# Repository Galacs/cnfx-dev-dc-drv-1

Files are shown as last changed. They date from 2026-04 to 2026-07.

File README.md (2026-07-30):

# CNFX Dev DC Driver 1

Dual 5V 1.5A DC motor driver for the cnfx series

## IC List

- STM32F103C8T6 (Main MCU)
- HT7533 (MCU 3v3 LDO)
- SN65HVD230DR (CAN transceiver)
- WS2812B (RGB addressable led)
- TPS259472 (+5V input efuse)
- DRV8837 (Integrated H-Bridge)

## Top preview



## Preview 3d render



## Pin definitions

```c

#define CAN_TX_PIN PA12
#define CAN_RX_PIN PA11
#define CAN_STATUS_PIN PA15

#define RGB_PIN PB13
#define ILM_PIN PB0
#define BTN_PIN PB12

#define SEL_0_PIN PB5
#define SEL_1_PIN PB6
#define SEL_2_PIN PB7

#define DC_1_SLEEP PA5
#define DC_1_IN1 PA6
#define DC_1_IN2 PA7

#define DC_1_SLEEP PA0
#define DC_1_IN1 PA1
#define DC_1_IN2 PA2
```

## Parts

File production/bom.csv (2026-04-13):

Designator | Footprint | Quantity | Value | LCSC Part #
C1, C16, C17 | 0402 | 3 | 1u | C52923
C10, C9 | 0603 | 2 | 20p | C1648
C11, C12, C14, C15, C18, C2, C21, C7 | 0402 | 8 | 0u1 | C307331
C13, C6, C8 | 0805 | 3 | 10u | C440198
C19, C20, C22, C23, C5 | 0805 | 5 | 22u | C45783
C4 | 0402 | 1 | 1n | C1523
D1 | LED_WS2812B_PLCC4_5.0x5.0mm_P3.2mm | 1 | WS2812B | C2874885
D2, D3, D4, D5, D7 | Diode_DFN1006 | 5 | H5VU10U | C22395519
D6 | 0805 | 1 | GREEN | C2297
D8 | 0805 | 1 | YELLOW | C2296
FB1 | 0805 | 1 | 600Ω@100M | C81034
J1 | JST_XH_B3B-XH-A_1x03_P2.50mm_Vertical | 1 | Conn_01x03
J3, J4, J6, J7 | JST_XH_B2B-XH-A_1x02_P2.50mm_Vertical | 4 | Conn_01x02
JP2, JP3, JP4 | SolderJumper-2_P1.3mm_Open_RoundedPad1.0x1.5mm | 3 | Jumper_2_Open
R1 | 1206 | 1 | 120 | C17909
R2 | 0402 | 1 | 820 | C25135
R3, R5, R8 | 0402 | 3 | 5k1 | C25905
R4, R6 | 0402 | 2 | 10k | C25744
R7 | 0603 | 1 | 560 | C23204
SW1, SW2, SW3 | SW_SPST_TS-1088-xR020 | 3 | SW_Push | C720477
TP1, TP2 | TestPoint_Keystone_5015_Micro_Mini | 2 | TestPoint | C2906768
U1 | SOIC-8_3.9x4.9mm_P1.27mm | 1 | SN65HVD230 | C12084
U2 | Texas_RPW0010A_VQFN-HR-10_2x2mm_P0.5mm | 1 | TPS259472A | C3662789
U3 | SOT-89-3 | 1 | HT753-1 | C14289
U4 | LQFP-48_7x7mm_P0.5mm | 1 | STM32F103C8Tx | C8734
U5, U6 | WSON-8-1EP_2x2mm_P0.5mm_EP0.9x1.6mm | 2 | DRV8837 | C39159
Y1 | Crystal_SMD_5032-2Pin_5.0x3.2mm | 1 | 8M | C115962

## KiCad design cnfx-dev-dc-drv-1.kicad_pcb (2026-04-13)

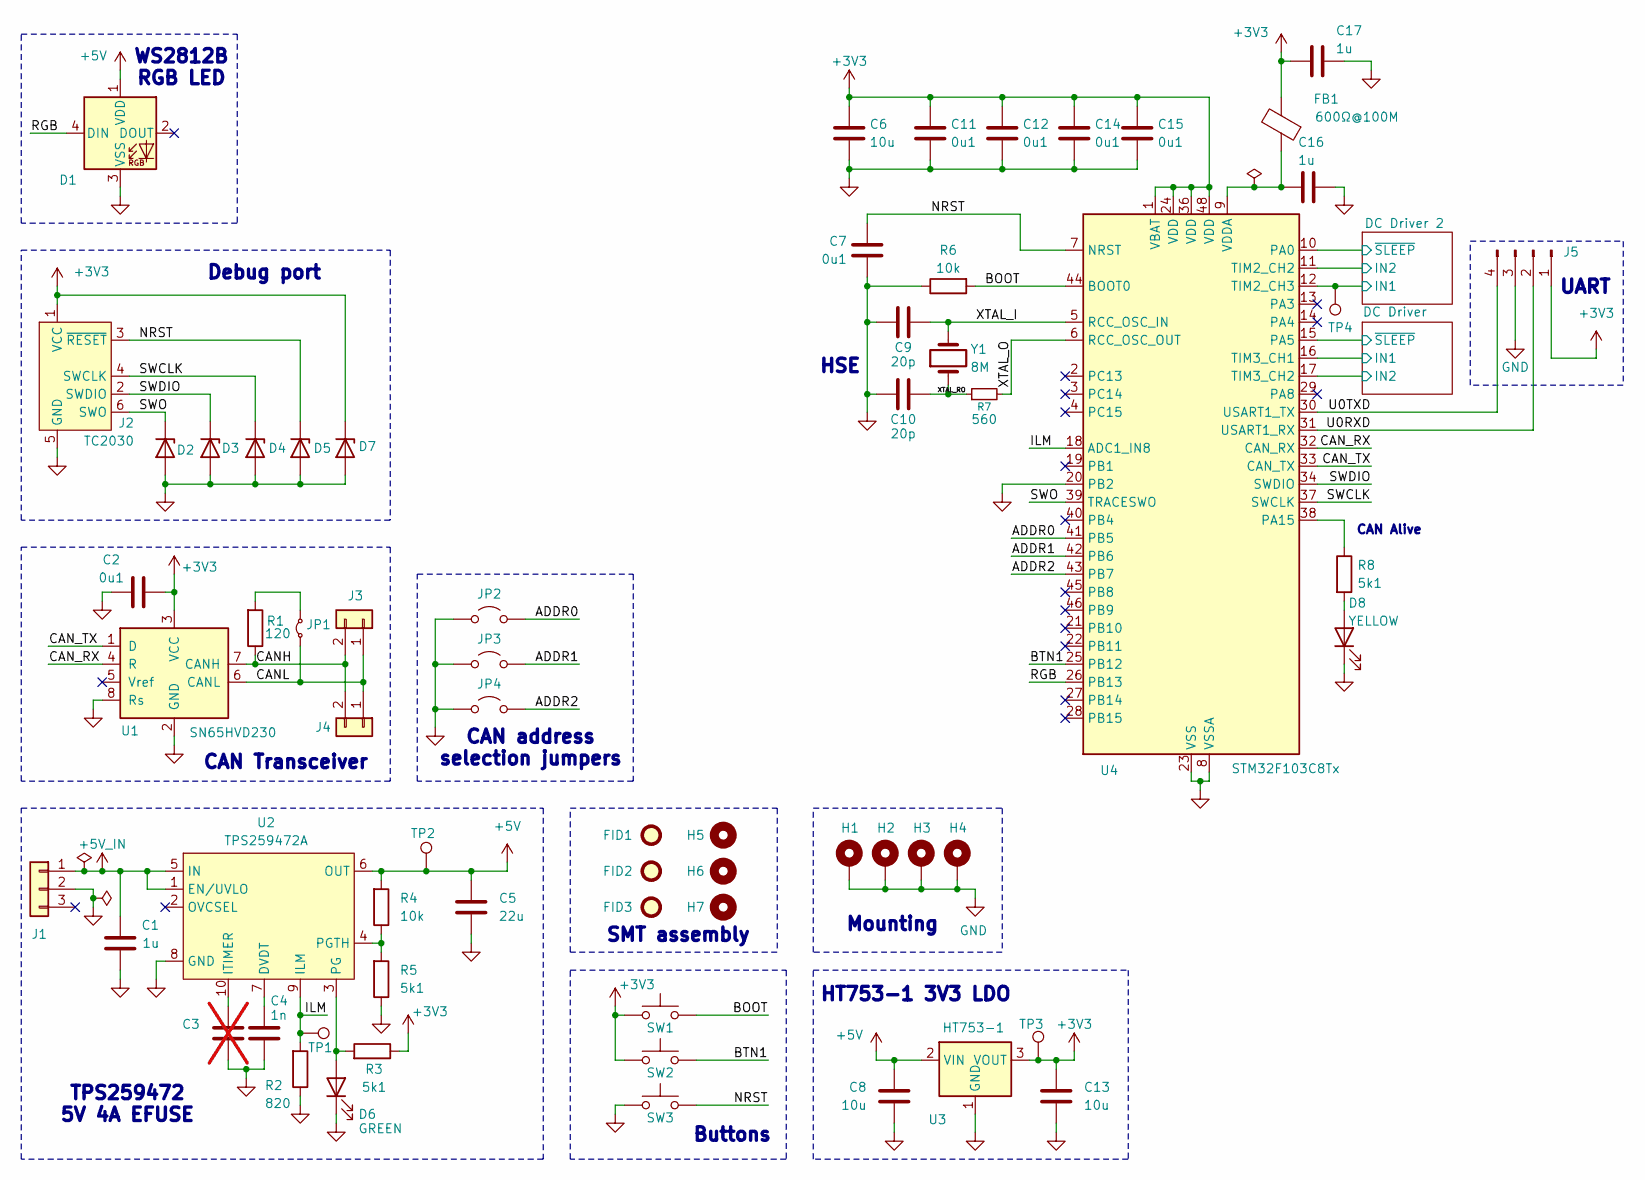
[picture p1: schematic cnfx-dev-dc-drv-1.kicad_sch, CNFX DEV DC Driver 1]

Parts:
C1, C16, C17: 1u; C_0402_1005Metric; Manufacturer Part Number CL05A105KA5NQNC; JLCPCB Part # C52923
C2, C7, C11, C12, C14, C15: 0u1; C_0402_1005Metric; Manufacturer Part Number CL05B104KB54PNC; JLCPCB Part # C307331
C3: C; C_0402_1005Metric; not fitted
C4: 1n; C_0402_1005Metric; Manufacturer Part Number 0402B102K500NT; JLCPCB Part # C1523
C5: 22u; C_0805_2012Metric; Manufacturer Part Number CL21A226MAQNNNE; JLCPCB Part # C45783
C6, C8, C13: 10u; C_0805_2012Metric; Manufacturer Part Number GRM21BR61H106KE43L; JLCPCB Part # C440198
C9, C10: 20p; C_0603_1608Metric; Manufacturer Part Number CL10C200JB8NNNC; JLCPCB Part # C1648
D1: WS2812B; LED_WS2812B_PLCC4_5.0x5.0mm_P3.2mm; Manufacturer Part Number WS2812B-V5/W; JLCPCB Part # C2874885
D2, D3, D4, D5, D7: H5VU10U; Diode_DFN1006; Manufacturer Part Number H5VU10U; JLCPCB Part # C22395519
D6: GREEN; LED_0805_2012Metric; Manufacturer Part Number KT-0805G; JLCPCB Part # C2297
D8: YELLOW; LED_0805_2012Metric; Manufacturer Part Number KT-0805Y; JLCPCB Part # C2296
FB1: 600Ω@100M; L_0805_2012Metric; Manufacturer Part Number MPZ2012S601ATD25; JLCPCB Part # C81034
FID1, FID2, FID3: Fiducial; Fiducial_1mm_Mask2mm
H1, H2, H3, H4: MountingHole_Pad; MountingHole_3.2mm_M3_Pad_Via
H5, H6, H7: MountingHole; ToolingHole_1.152mm
J1: Conn_01x03; JST_XH_B3B-XH-A_1x03_P2.50mm_Vertical
J2: TC2030; Tag-Connect_TC2030-IDC-NL_2x03_P1.27mm_Vertical
J3, J4: Conn_01x02; JST_XH_B2B-XH-A_1x02_P2.50mm_Vertical
J5: Conn_01x04_Pin; PinHeader_1x04_P2.54mm_Vertical
JP1: Jumper_2_Small_Bridged; PinHeader_1x02_P2.54mm_Vertical
JP2, JP3, JP4: Jumper_2_Open; SolderJumper-2_P1.3mm_Open_RoundedPad1.0x1.5mm
R1: 120; R_1206_3216Metric; Manufacturer Part Number 1206W4F1200T5E; JLCPCB Part # C17909
R2: 820; R_0402_1005Metric; Manufacturer Part Number 0402WGF8200TCE; JLCPCB Part # C25135
R3, R5, R8: 5k1; R_0402_1005Metric; Manufacturer Part Number 0402WGF5101TCE; JLCPCB Part # C25905
R4, R6: 10k; R_0402_1005Metric; Manufacturer Part Number 0402WGF1002TCE; JLCPCB Part # C25744
R7: 560; R_0603_1608Metric; Manufacturer Part Number 0603WAF5600T5E; JLCPCB Part # C23204
SW1, SW2, SW3: SW_Push; SW_SPST_TS-1088-xR020; Manufacturer Part Number TS-1088-AR02016; JLCPCB Part # C720477
TP1, TP2: TestPoint; TestPoint_Keystone_5015_Micro_Mini; Manufacturer Part Number 5015; JLCPCB Part # C2906768
TP3, TP4: TestPoint; TestPoint_Pad_D2.0mm
U1: SN65HVD230; SOIC-8_3.9x4.9mm_P1.27mm; Manufacturer Part Number SN65HVD230DR; JLCPCB Part # C12084
U2: TPS259472A; Texas_RPW0010A_VQFN-HR-10_2x2mm_P0.5mm; Manufacturer Part Number TPS259472ARPWR; JLCPCB Part # C3662789
U3: HT753-1; SOT-89-3; Manufacturer Part Number HT7533-1; JLCPCB Part # C14289
U4: STM32F103C8Tx; LQFP-48_7x7mm_P0.5mm; Manufacturer Part Number STM32F103C8T6; JLCPCB Part # C8734
Y1: 8M; Crystal_SMD_5032-2Pin_5.0x3.2mm; Manufacturer Part Number X50328MSB2GI; JLCPCB Part # C115962

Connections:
+3V3: C2.1, C6.1, C11.1, C12.1, C13.1, C14.1, C15.1, C17.1, D7.1 (K), FB1.2, J2.1 (VCC), J5.1, R3.1, SW1.1, SW2.1, TP3.1 (1_1), U1.3 (VCC), U3.3 (VOUT), U4.1 (VBAT), U4.24 (VDD), U4.36 (VDD), U4.48 (VDD); also elsewhere on the board
+5V: C5.1, C8.1, D1.1 (VDD), R4.2, TP2.1 (1_1), U2.6 (OUT), U3.2 (VIN); also elsewhere on the board
+5V_IN: C1.2, J1.1, U2.1 (EN/UVLO), U2.5 (IN)
/ADDR0: JP2.2 (B), U4.41 (PB5)
/ADDR1: JP3.2 (B), U4.42 (PB6)
/ADDR2: JP4.2 (B), U4.43 (PB7)
/BOOT: R6.2, SW1.2, U4.44 (BOOT0)
/BTN1: SW2.2, U4.25 (PB12)
/CANH: J3.2, J4.2, R1.1, U1.7 (CANH)
/CANL: J3.1, J4.1, JP1.1 (A), U1.6 (CANL)
/CAN_RX: U1.4 (R), U4.32 (CAN_RX)
/CAN_TX: U1.1 (D), U4.33 (CAN_TX)
/DC Driver 2/IN1: TP4.1 (1_1), U4.12 (TIM2_CH3); also elsewhere on the board
/DC Driver 2/IN2: U4.11 (TIM2_CH2); also elsewhere on the board
/DC Driver 2/~SLEEP: U4.10 (PA0); also elsewhere on the board
/DC Driver/IN1: U4.16 (TIM3_CH1); also elsewhere on the board
/DC Driver/IN2: U4.17 (TIM3_CH2); also elsewhere on the board
/DC Driver/~SLEEP: U4.15 (PA5); also elsewhere on the board
/ILM: R2.2, TP1.1 (1_1), U2.9 (ILM), U4.18 (ADC1_IN8)
/NRST: C7.1, D5.1 (K), J2.3 (~RESET), SW3.2, U4.7 (NRST)
/RGB: D1.4 (DIN), U4.26 (PB13)
/SWCLK: D4.1 (K), J2.4 (SWCLK), U4.37 (SWCLK)
/SWDIO: D3.1 (K), J2.2 (SWDIO), U4.34 (SWDIO)
/SWO: D2.1 (K), J2.6 (SWO), U4.39 (TRACESWO)
/U0RXD: J5.2, U4.31 (USART1_RX)
/U0TXD: J5.4, U4.30 (USART1_TX)
/XTAL_I: C9.1, U4.5 (RCC_OSC_IN), Y1.2
/XTAL_O: R7.2, U4.6 (RCC_OSC_OUT)
/XTAL_RO: C10.1, R7.1, Y1.1
GND: C1.1, C2.2, C3.2, C4.2, C5.2, C6.2, C7.2, C8.2, C9.2, C10.2, C11.2, C12.2, C13.2, C14.2, C15.2, C16.2, C17.2, D1.3 (VSS), D2.2 (A), D3.2 (A), D4.2 (A), D5.2 (A), D6.1 (K), D7.2 (A), D8.1 (K), H1.1 (1_1), H2.1 (1_1), H3.1 (1_1), H4.1 (1_1), J1.2, J2.5 (GND), J5.3, JP2.1 (A), JP3.1 (A), JP4.1 (A), R2.1, R5.1, R6.1, SW3.1, U1.2 (GND), U1.8 (Rs), U2.8 (GND), U3.1 (GND), U4.8 (VSSA), U4.20 (PB2), U4.23 (VSS), U4.35 (VSS), U4.47 (VSS); also elsewhere on the board
unnamed: D6.2 (A), R3.2, U2.3 (PG)
unnamed: D8.2 (A), R8.2
unnamed: JP1.2 (B), R1.2
unnamed: C4.1, U2.7 (DVDT)
unnamed: C3.1, U2.10 (ITIMER)
unnamed: R4.1, R5.2, U2.4 (PGTH)
unnamed: R8.1, U4.38 (PA15)
unnamed: C16.1, FB1.1, U4.9 (VDDA)

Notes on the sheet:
HSE
CAN address selection jumpers
Debug port
SMT assembly
Mounting
CAN Transceiver
UART
TPS259472 5V 4A EFUSE
HT753-1 3V3 LDO
Buttons
WS2812B RGB LED
CAN Alive

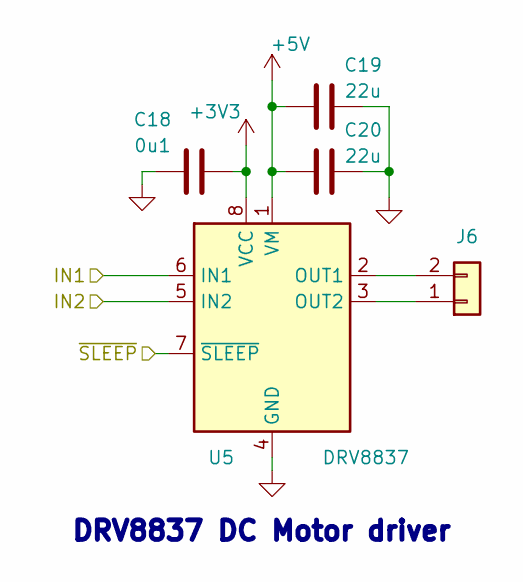
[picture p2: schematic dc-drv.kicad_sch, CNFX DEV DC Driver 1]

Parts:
C18: 0u1; C_0402_1005Metric; Manufacturer Part Number CL05B104KB54PNC; JLCPCB Part # C307331
C19, C20: 22u; C_0805_2012Metric; Manufacturer Part Number CL21A226MAQNNNE; JLCPCB Part # C45783
J6: Conn_01x02; JST_XH_B2B-XH-A_1x02_P2.50mm_Vertical
U5: DRV8837; WSON-8-1EP_2x2mm_P0.5mm_EP0.9x1.6mm; Manufacturer Part Number DRV8837DSGR; JLCPCB Part # C39159

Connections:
+3V3: C18.2, U5.8 (VCC); also elsewhere on the board
+5V: C19.2, C20.2, U5.1 (VM); also elsewhere on the board
/DC Driver/IN1: U5.6 (IN1); also elsewhere on the board
/DC Driver/IN2: U5.5 (IN2); also elsewhere on the board
/DC Driver/~SLEEP: U5.7 (~SLEEP); also elsewhere on the board
GND: C18.1, C19.1, C20.1, U5.4 (GND), U5.9 (GND); also elsewhere on the board
unnamed: J6.1, U5.3 (OUT2)
unnamed: J6.2, U5.2 (OUT1)

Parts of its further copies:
C21: 0u1; C_0402_1005Metric; Manufacturer Part Number CL05B104KB54PNC; JLCPCB Part # C307331
C22, C23: 22u; C_0805_2012Metric; Manufacturer Part Number CL21A226MAQNNNE; JLCPCB Part # C45783
J7: Conn_01x02; JST_XH_B2B-XH-A_1x02_P2.50mm_Vertical
U6: DRV8837; WSON-8-1EP_2x2mm_P0.5mm_EP0.9x1.6mm; Manufacturer Part Number DRV8837DSGR; JLCPCB Part # C39159

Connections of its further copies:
+3V3: C21.2, U6.8 (VCC); also elsewhere on the board
+5V: C22.2, C23.2, U6.1 (VM); also elsewhere on the board
/DC Driver 2/IN1: U6.6 (IN1); also elsewhere on the board
/DC Driver 2/IN2: U6.5 (IN2); also elsewhere on the board
/DC Driver 2/~SLEEP: U6.7 (~SLEEP); also elsewhere on the board
GND: C21.1, C22.1, C23.1, U6.4 (GND), U6.9 (GND); also elsewhere on the board
unnamed: J7.1, U6.3 (OUT2)
unnamed: J7.2, U6.2 (OUT1)

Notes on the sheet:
DRV8837 DC Motor driver

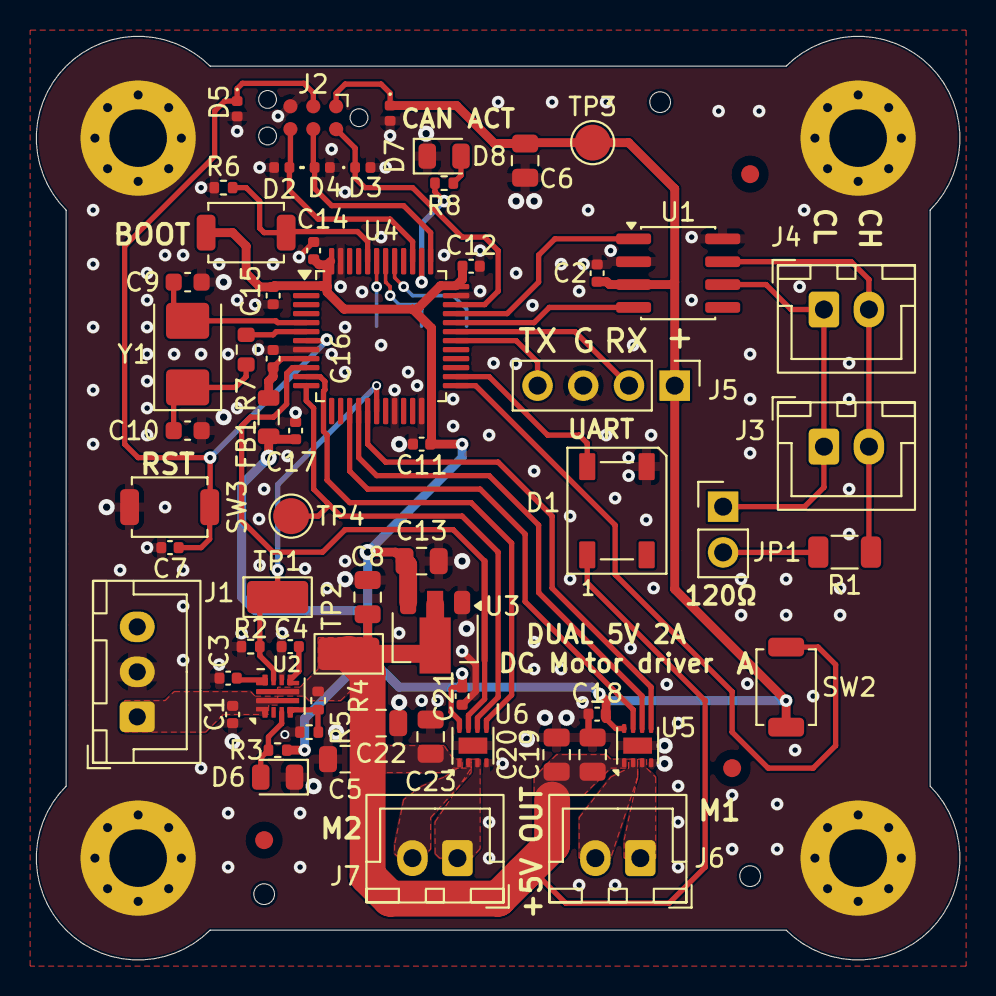
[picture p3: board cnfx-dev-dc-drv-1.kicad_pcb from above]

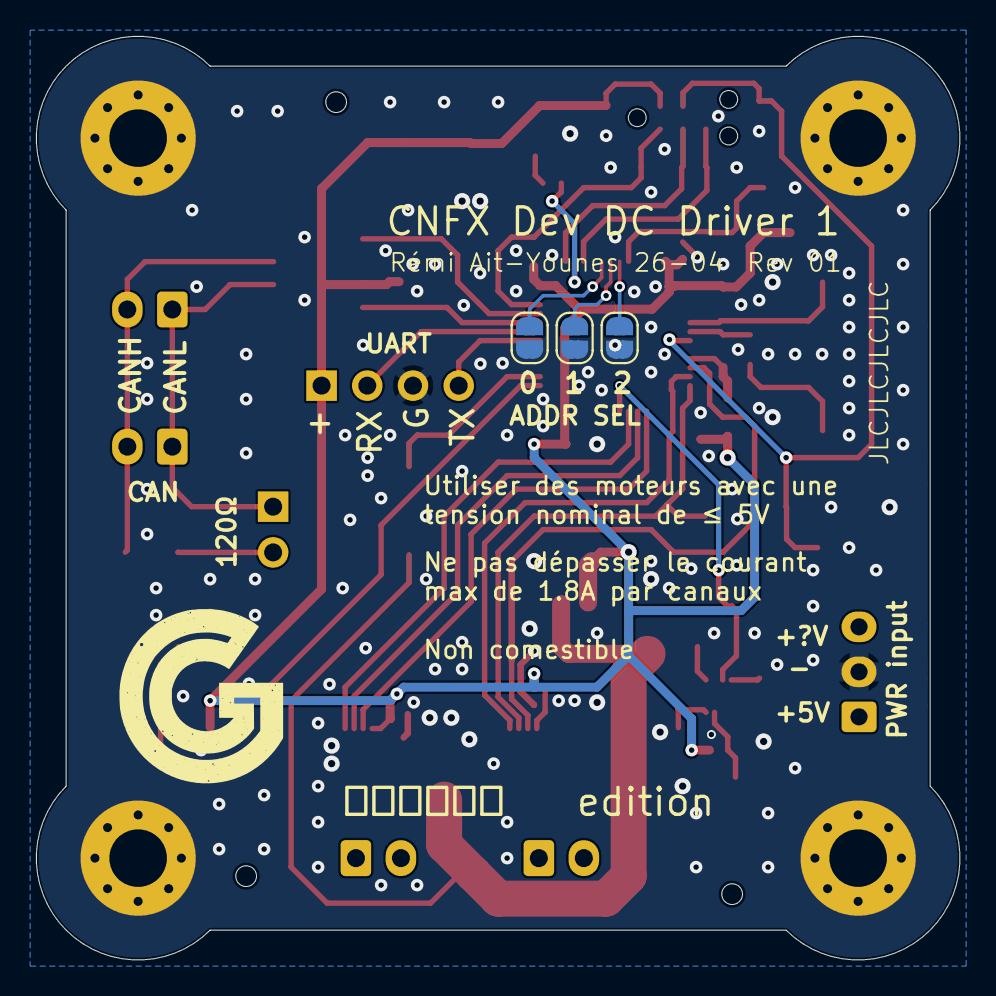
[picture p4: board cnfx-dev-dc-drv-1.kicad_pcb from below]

Board: 2 copper layers, 51.3 x 51.3 mm, 75 parts (3 on the bottom side), 42 nets.

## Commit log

2026-04-11 schem: import STM32F103 from mhadb-2208-bldc-drv
    [cnfx-dev-dc-drv-1.kicad_sch]
2026-04-11 schem: add BOOT/RST and misc btns
    [cnfx-dev-dc-drv-1.kicad_sch]
2026-04-11 schem: import TC2030 debug connector
    [cnfx-dev-dc-drv-1.kicad_sch]
2026-04-11 schem: add spare gpios
    [cnfx-dev-dc-drv-1.kicad_sch]
2026-04-11 schem: add RGB status led
    [cnfx-dev-dc-drv-1.kicad_sch]
2026-04-11 schem: import CAN transceiver
    [cnfx-dev-dc-drv-1.kicad_sch]
2026-04-11 schem: add CAN connectors
    [cnfx-dev-dc-drv-1.kicad_sch]
2026-04-11 schem: add DRV8837 dc motor drivers
    [cnfx-dev-dc-drv-1.kicad_sch, dc-drv.kicad_sch]
2026-04-11 schem: remove unused i2c pullups
    [cnfx-dev-dc-drv-1.kicad_sch]
2026-04-11 schem: import HT753-1 3V3 100mA LDO
    [cnfx-dev-dc-drv-1.kicad_sch]
2026-04-11 schem: add TPS259472 5V 4A efuse
    [cnfx-dev-dc-drv-1.kicad_sch]
2026-04-11 schem: change rgb led +5V supply
    [cnfx-dev-dc-drv-1.kicad_sch]
2026-04-11 schem: add UART connector
    [cnfx-dev-dc-drv-1.kicad_sch]
2026-04-11 schem: connect DC drivers to stm32
    [cnfx-dev-dc-drv-1.kicad_sch]
2026-04-11 schem: reorganize
    [cnfx-dev-dc-drv-1.kicad_sch]
2026-04-11 schem: connect rgb pin to stm32
    [cnfx-dev-dc-drv-1.kicad_sch]
2026-04-11 schem: fix efuse en pin
    [cnfx-dev-dc-drv-1.kicad_sch]
2026-04-11 schem: add test points
    [cnfx-dev-dc-drv-1.kicad_sch, dc-drv.kicad_sch]
2026-04-11 schem: run and fix ERC
    [cnfx-dev-dc-drv-1.kicad_sch]
2026-04-11 schem: add ordering info to BOM
    [dc-drv.kicad_sch]
2026-04-11 schem: add title
    [cnfx-dev-dc-drv-1.kicad_sch]
2026-04-11 schem: reannotate
    [cnfx-dev-dc-drv-1.kicad_sch, dc-drv.kicad_sch]
2026-04-11 pcb: create file
    [cnfx-dev-dc-drv-1.kicad_pcb]
2026-04-11 pcb: import two layer stackup and constraints
    [cnfx-dev-dc-drv-1.kicad_pcb]
2026-04-11 pcb: import footprints from schem
    [cnfx-dev-dc-drv-1.kicad_pcb]
2026-04-11 schem: remove extra gpios
    [cnfx-dev-dc-drv-1.kicad_pcb, cnfx-dev-dc-drv-1.kicad_sch]
2026-04-11 schem: add ILM efuse reading to stm32
    [cnfx-dev-dc-drv-1.kicad_sch]
2026-04-11 pcb: add initial layout
    [cnfx-dev-dc-drv-1.kicad_pcb]
2026-04-11 schem/pcb: add mounting holes
    [cnfx-dev-dc-drv-1.kicad_sch]
2026-04-11 pcb: refine layout
    [cnfx-dev-dc-drv-1.kicad_pcb]
2026-04-11 pcb: add board outline
    [cnfx-dev-dc-drv-1.kicad_pcb]
2026-04-11 pcb: add grid/place origin
    [cnfx-dev-dc-drv-1.kicad_pcb]
2026-04-11 pcb: final layout
    [cnfx-dev-dc-drv-1.kicad_pcb]
2026-04-11 pcb: add gnd vias
    [cnfx-dev-dc-drv-1.kicad_pcb]
2026-04-11 pcb: add XTAL routing
    [cnfx-dev-dc-drv-1.kicad_pcb]
2026-04-11 pcb: add SWD routing
    [cnfx-dev-dc-drv-1.kicad_pcb]
2026-04-11 pcb: add can routing
    [cnfx-dev-dc-drv-1.kicad_pcb]
2026-04-11 pcb: add UART routing
    [cnfx-dev-dc-drv-1.kicad_pcb]
2026-04-11 pcb: add DC drivers routing
    [cnfx-dev-dc-drv-1.kicad_pcb, cnfx-dev-dc-drv-1.kicad_sch, dc-drv.kicad_sch]
2026-04-11 pcb: add efuse routing
    [cnfx-dev-dc-drv-1.kicad_pcb]
2026-04-11 pcb: add dc drivers sleep pin routing
    [cnfx-dev-dc-drv-1.kicad_pcb]
2026-04-11 pcb: add +5V pwr routing
    [cnfx-dev-dc-drv-1.kicad_pcb]
2026-04-11 pcb: add +3V3 pwr routing
    [cnfx-dev-dc-drv-1.kicad_pcb]
2026-04-11 pcb: add RGB and btns routing
    [cnfx-dev-dc-drv-1.kicad_pcb, cnfx-dev-dc-drv-1.kicad_sch]
2026-04-11 pcb: add can status led routing
    [cnfx-dev-dc-drv-1.kicad_pcb]
2026-04-11 pcb: add stitching vias
    [cnfx-dev-dc-drv-1.kicad_pcb]
2026-04-11 pcb(silk): clean up reference designators
    [cnfx-dev-dc-drv-1.kicad_pcb]
2026-04-11 pcb(silk): add user txt
    [cnfx-dev-dc-drv-1.kicad_pcb]
2026-04-11 pcb: run and fix DRC
    [cnfx-dev-dc-drv-1.kicad_pcb]
2026-04-11 pcb: add title
    [cnfx-dev-dc-drv-1.kicad_pcb, dc-drv.kicad_sch]
2026-04-11 generate production files
    [bom.csv, designators.csv, positions.csv]
2026-04-12 schem/pcb: add smt fiducials and tooling holes
    [cnfx-dev-dc-drv-1.kicad_pcb, cnfx-dev-dc-drv-1.kicad_sch]
2026-04-12 schem/pcb: add can addr selection jumpers
    [cnfx-dev-dc-drv-1.kicad_pcb, cnfx-dev-dc-drv-1.kicad_sch]
2026-04-12 regenerate production files
    [bom.csv, cnfx-dev-dc-drv-1.kicad_pcb, designators.csv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]
2026-04-13 schem/pcb: change 22u capactior footprint
    [cnfx-dev-dc-drv-1.kicad_pcb, cnfx-dev-dc-drv-1.kicad_sch]
2026-04-13 schem/pcb: update dc drivers 22u bulk footprints
    [cnfx-dev-dc-drv-1.kicad_pcb, dc-drv.kicad_sch]
